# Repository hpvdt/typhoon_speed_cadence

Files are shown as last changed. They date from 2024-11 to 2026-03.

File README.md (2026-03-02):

# Typhoon Speed and Cadence

This is the amazing repository for the amazing Speed and Cadance team.
This embedded system uses an STM32 and a hall effect setup to accurately calculate the speed of the bike in real time, displaying the information to an OLED
HOE: Oliver Cai, Juston Lo
Lead: Daniel Dot
Members: Luca M, Rena, Noah, Iris

MEMBERS ADD YOUR LAST NAMES PLEASE I DONT KNOW THEM :(

## Hardware Setup

We must all operate on the same main version of KiCad, 9.0.
Ensure you are always working on the project file, never open the files standalone.

## Firmware Setup

### THIS PART IS VERY IMPORTANT PLEASE READ

We must all operate on the same versions, if we do not then stuff will break. We are currently using:
- STM32CubeIDE 2.0.0
- STM32CubeMX 6.16.0

You must download both to program as the IDE is used oto program while the CubeMX is for the .ioc file to configure the board pinout.

When writing code in the main.c, main.h, or any program where code is overwritten from the .ioc save, PLEASE ENSURE YOU ARE WRITING IN A USER CODE BLOCK, or else your code will be removed.

The main code is found in main.c in the src folder, and whenever working on the code always work in the project folder, dont open the file standalone. 
The logic for the code is commented in code, and any changes MUST also be commented for others to work simultaneously on it.

If there are any questions about the project, message me on disc dot2944, or email daniel.dot@mail.utoronto.ca

## Organization

Pretty self-explanitory, put hardware related files into the `hardware` folder, firmware in the `firmware` folder. Other folders can be added as needed: for example a `media` folder is handy for storing pictures related to a project which can be used in documentation.

## Conventions

Partly for consistency, partly for functionality; please follow the following conventions:

- Try to keep folder names to single words and all lowercase
- Use underscores to separate words in names (e.g. `board_rev1`). **DO NOT USE SPACES! ESPECIALLY FOR FOLDERS CONTAINING CODE!** Spaces in file paths may cause issues in compilers and such so best to avoid them entirely.

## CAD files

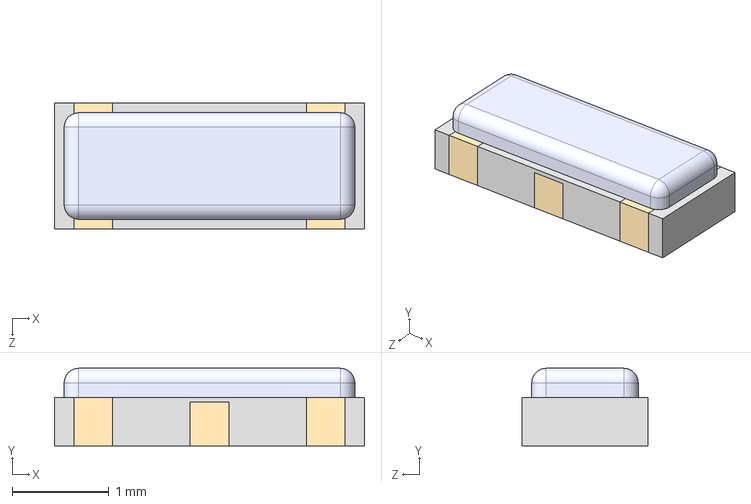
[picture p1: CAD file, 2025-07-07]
hardware/vers_2/CSTNE8M00G52Z000R0/CSTNE8M00G52Z000R0.step
3.20 x 0.8 x 1.30 mm

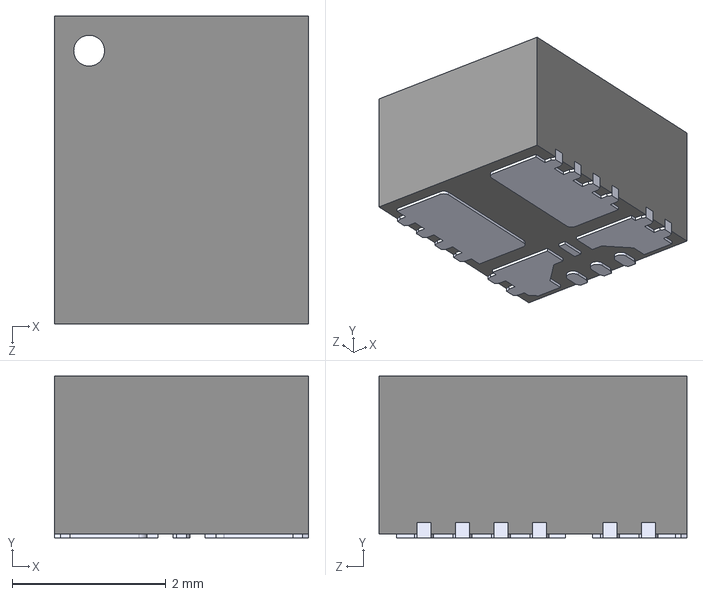
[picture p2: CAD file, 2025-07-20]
hardware/vers_2/TPSM861253RDXR/TPSM861253RDXR.step
3.30 x 2.10 x 4.00 mm

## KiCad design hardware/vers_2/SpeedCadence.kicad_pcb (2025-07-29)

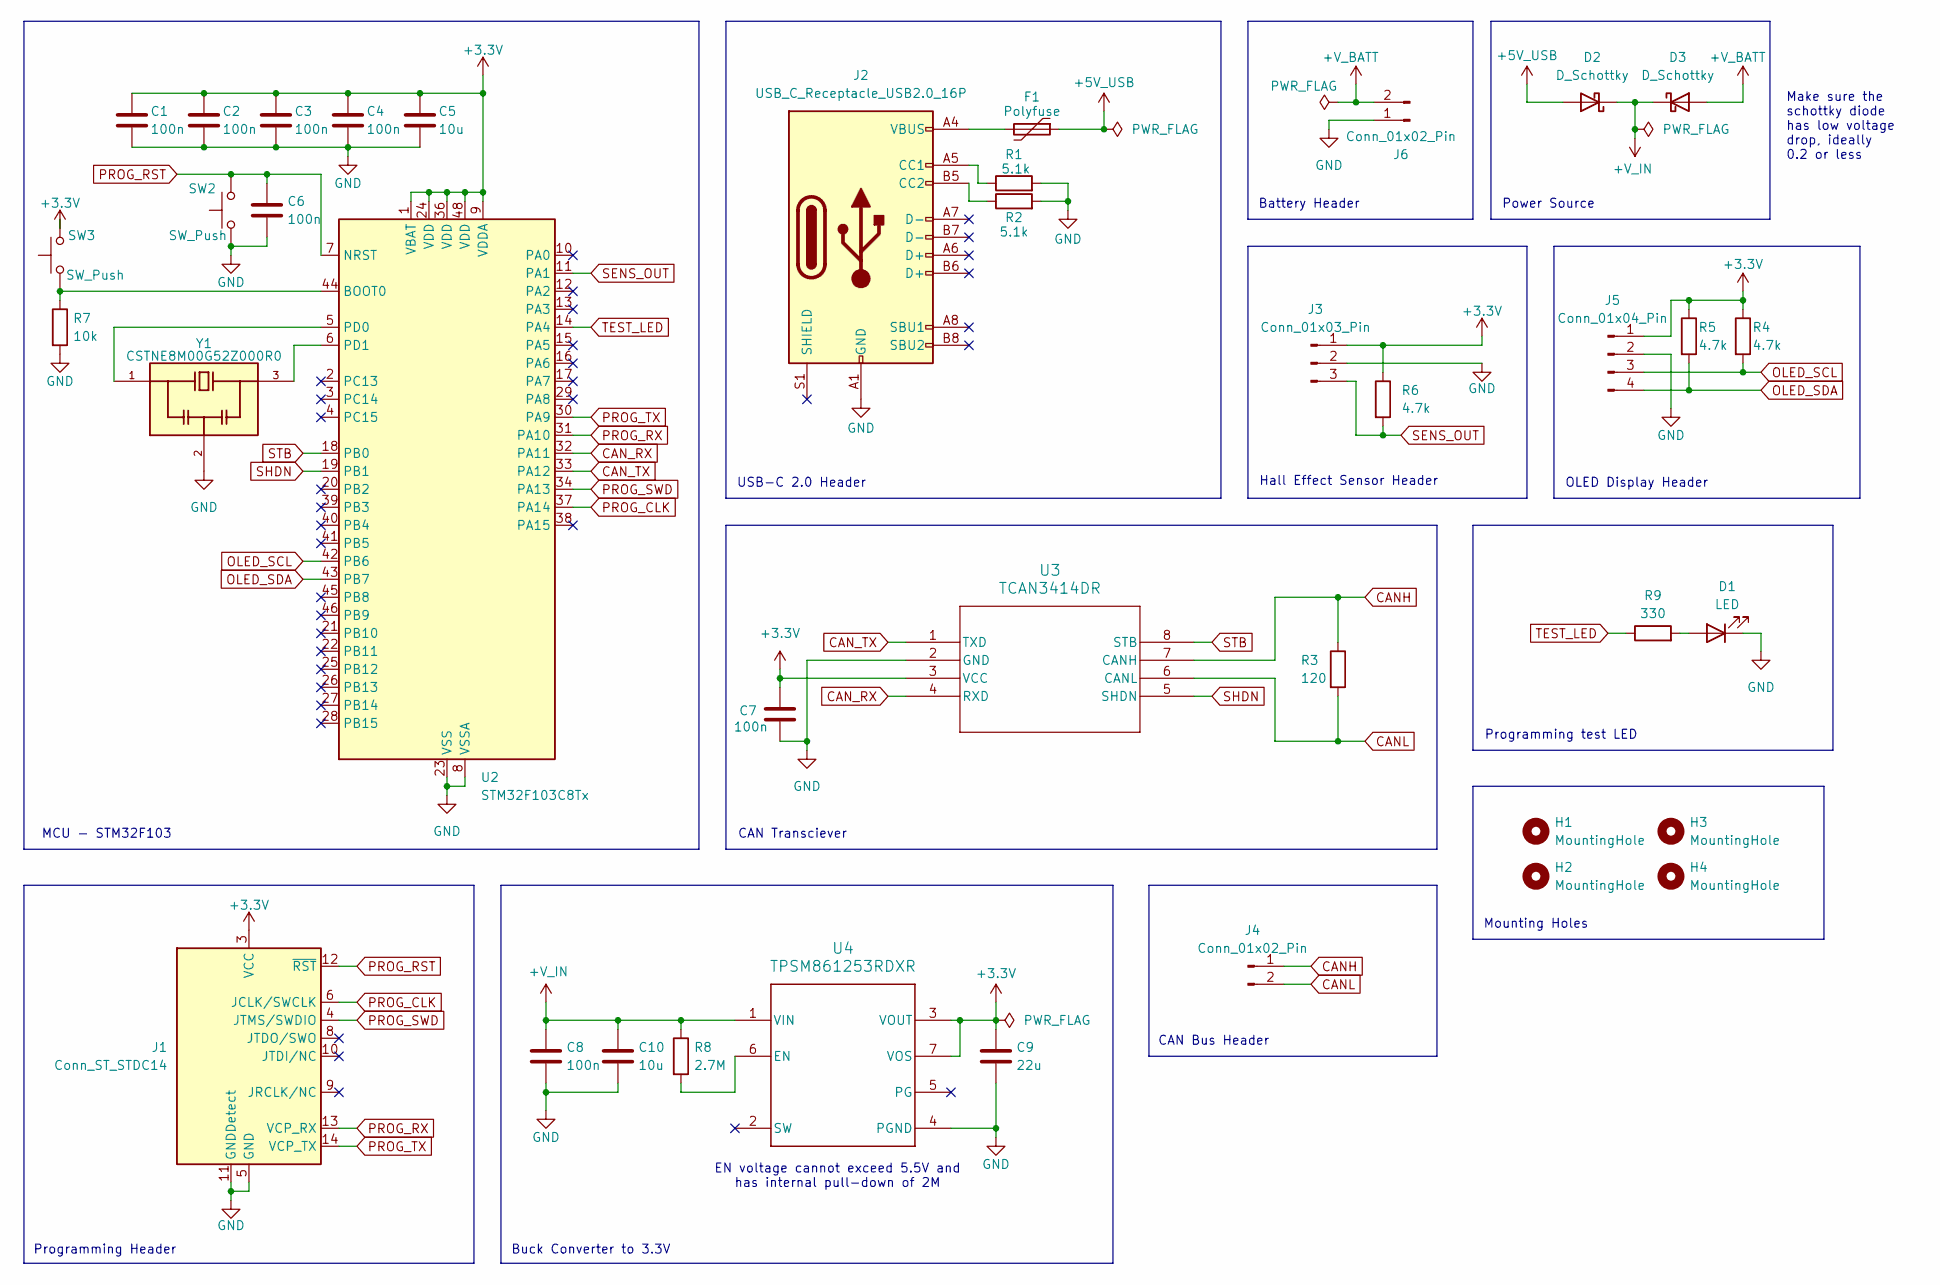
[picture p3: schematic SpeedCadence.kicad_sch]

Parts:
C1, C2, C3, C4, C6, C7, C8: 100n; C_0805_2012Metric; Manufacturer Part Number CC0805KRX7R9BB104
C5, C10: 10u; C_0805_2012Metric; Manufacturer Part Number GRM21BR71A106KA73K
C9: 22u; C_0805_2012Metric; Manufacturer Part Number GRM21BZ71A226ME15L
D1: LED; LED_0805_2012Metric; Manufacturer Part Number 5975906507F
D2, D3: D_Schottky; D_SOD-123; Manufacturer Part Number 1N5819HW-7-F
F1: Polyfuse; Fuse_1206_3216Metric; Manufacturer Part Number 0ZCJ0020FF2E
H1, H2, H3, H4: MountingHole; MountingHole_2.2mm_M2
J1: Conn_ST_STDC14; PinHeader_2x07_P1.27mm_Vertical_SMD; Manufacturer Part Number FTSH-107-01-L-DV-K-A
J2: USB_C_Receptacle_USB2.0_16P; USB_C_Receptacle_JAE_DX07S016JA1R1500; Manufacturer Part Number DX07S016JA3R1500
J3: Conn_01x03_Pin; JST_XH_B3B-XH-A_1x03_P2.50mm_Vertical; Manufacturer Part Number B3B-XH-A(LF)(SN)
J4, J6: Conn_01x02_Pin; JST_XH_B2B-XH-A_1x02_P2.50mm_Vertical; Manufacturer Part Number B2B-XH-A-BK(LF)(SN)
J5: Conn_01x04_Pin; JST_XH_B4B-XH-A_1x04_P2.50mm_Vertical; Manufacturer Part Number B4B-XH-A(LF)(SN)
R1, R2: 5.1k; R_0805_2012Metric; Manufacturer Part Number RC0805JR-075K1L
R3: 120; R_0805_2012Metric; Manufacturer Part Number P0603Y60R0BBT
R4, R5, R6: 4.7k; R_0805_2012Metric
R7: 10k; R_0805_2012Metric
R8: 2.7M; R_0805_2012Metric
R9: 330; R_0805_2012Metric
SW2, SW3: SW_Push; SW_SPST_SKQG_WithStem
U2: STM32F103C8Tx; LQFP-48_7x7mm_P0.5mm
U3: TCAN3414DR; SOIC-8_3.9x4.9mm_P1.27mm
U4: TPSM861253RDXR; VREG_TPSM861253RDXR
Y1: CSTNE8M00G52Z000R0; OSC_CSTNE8M00G52Z000R0; PARTREV JGC42-8858A

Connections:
+3.3V: C1.2, C2.2, C3.2, C4.2, C5.1, C7.1, C9.1, J1.3 (VCC), J3.1, J5.1, R4.1, R5.1, R6.1, SW3.2, U2.1 (VBAT), U2.9 (VDDA), U2.24 (VDD), U2.36 (VDD), U2.48 (VDD), U3.3 (VCC), U4.3 (VOUT), U4.7 (VOS), U4.14, U4.15, U4.16, U4.17, U4.18, U4.19
+5V_USB: D2.2 (A), F1.1
+V_BATT: D3.2 (A), J6.2
+V_IN: C8.1, C10.1, D2.1 (K), D3.1 (K), R8.1, U4.1 (VIN)
CANH: J4.1, R3.1, U3.7 (CANH)
CANL: J4.2, R3.2, U3.6 (CANL)
CAN_RX: U2.32 (PA11), U3.4 (RXD)
CAN_TX: U2.33 (PA12), U3.1 (TXD)
GND: C1.1, C2.1, C3.1, C4.1, C5.2, C6.2, C7.2, C8.2, C9.2, C10.2, D1.1 (K), J1.5 (GND), J1.7 (GND), J1.11 (GNDDetect), J2.A1 (GND), J2.A12 (GND), J2.B1 (GND), J2.B12 (GND), J3.2, J5.2, J6.1, R1.2, R2.2, R7.2, SW2.1, U2.8 (VSSA), U2.23 (VSS), U2.35 (VSS), U2.47 (VSS), U3.2 (GND), U4.4 (PGND), Y1.2
unnamed: D1.2 (A), R9.2
unnamed: F1.2, J2.A4 (VBUS), J2.A9 (VBUS), J2.B4 (VBUS), J2.B9 (VBUS)
unnamed: J2.A5 (CC1), R1.1
unnamed: J2.B5 (CC2), R2.1
unnamed: R7.1, SW3.1, U2.44 (BOOT0)
unnamed: U2.5 (PD0), Y1.1
unnamed: U2.6 (PD1), Y1.3
unnamed: R8.2, U4.6 (EN)
OLED_SCL: J5.3, R4.2, U2.42 (PB6)
OLED_SDA: J5.4, R5.2, U2.43 (PB7)
PROG_CLK: J1.6 (JCLK/SWCLK), U2.37 (PA14)
PROG_RST: C6.1, J1.12 (~RST), SW2.2, U2.7 (NRST)
PROG_RX: J1.13 (VCP_RX), U2.31 (PA10)
PROG_SWD: J1.4 (JTMS/SWDIO), U2.34 (PA13)
PROG_TX: J1.14 (VCP_TX), U2.30 (PA9)
SENS_OUT: J3.3, R6.2, U2.11 (PA1)
SHDN: U2.19 (PB1), U3.5 (SHDN)
STB: U2.18 (PB0), U3.8 (STB)
TEST_LED: R9.1, U2.14 (PA4)

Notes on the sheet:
Mounting Holes
CAN Transciever
MCU - STM32F103
CAN Bus Header
Battery Header
USB-C 2.0 Header
Buck Converter to 3.3V
Power Source
Hall Effect Sensor Header
EN voltage cannot exceed 5.5V and has internal pull-down of 2M
OLED Display Header
Programming Header
Programming test LED
Make sure the schottky diode has low voltage drop, ideally 0.2 or less

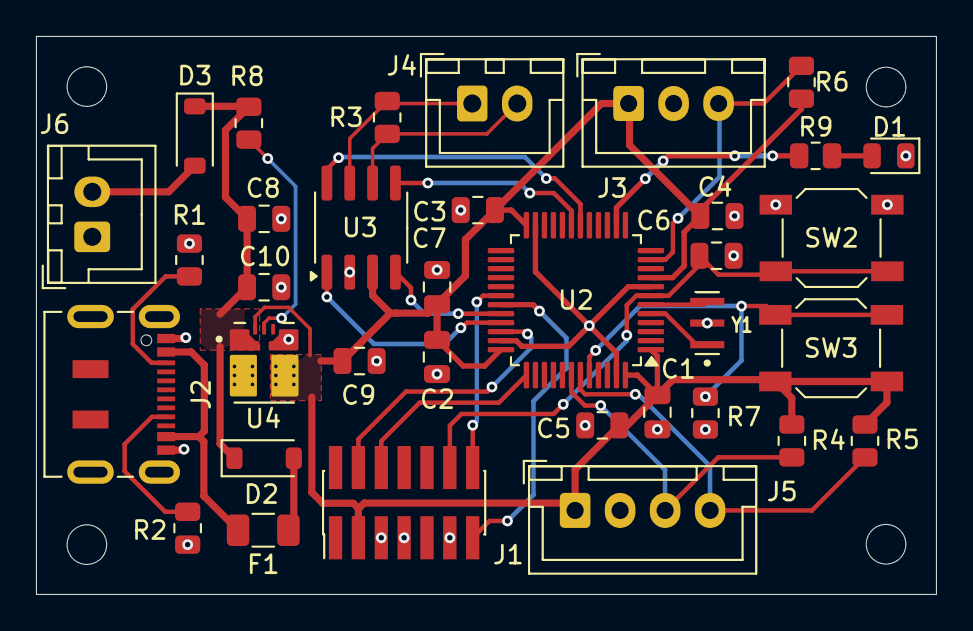
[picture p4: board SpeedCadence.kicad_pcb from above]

Board: 2 copper layers, 50.0 x 31.0 mm, 39 parts (0 on the bottom side), 28 nets.

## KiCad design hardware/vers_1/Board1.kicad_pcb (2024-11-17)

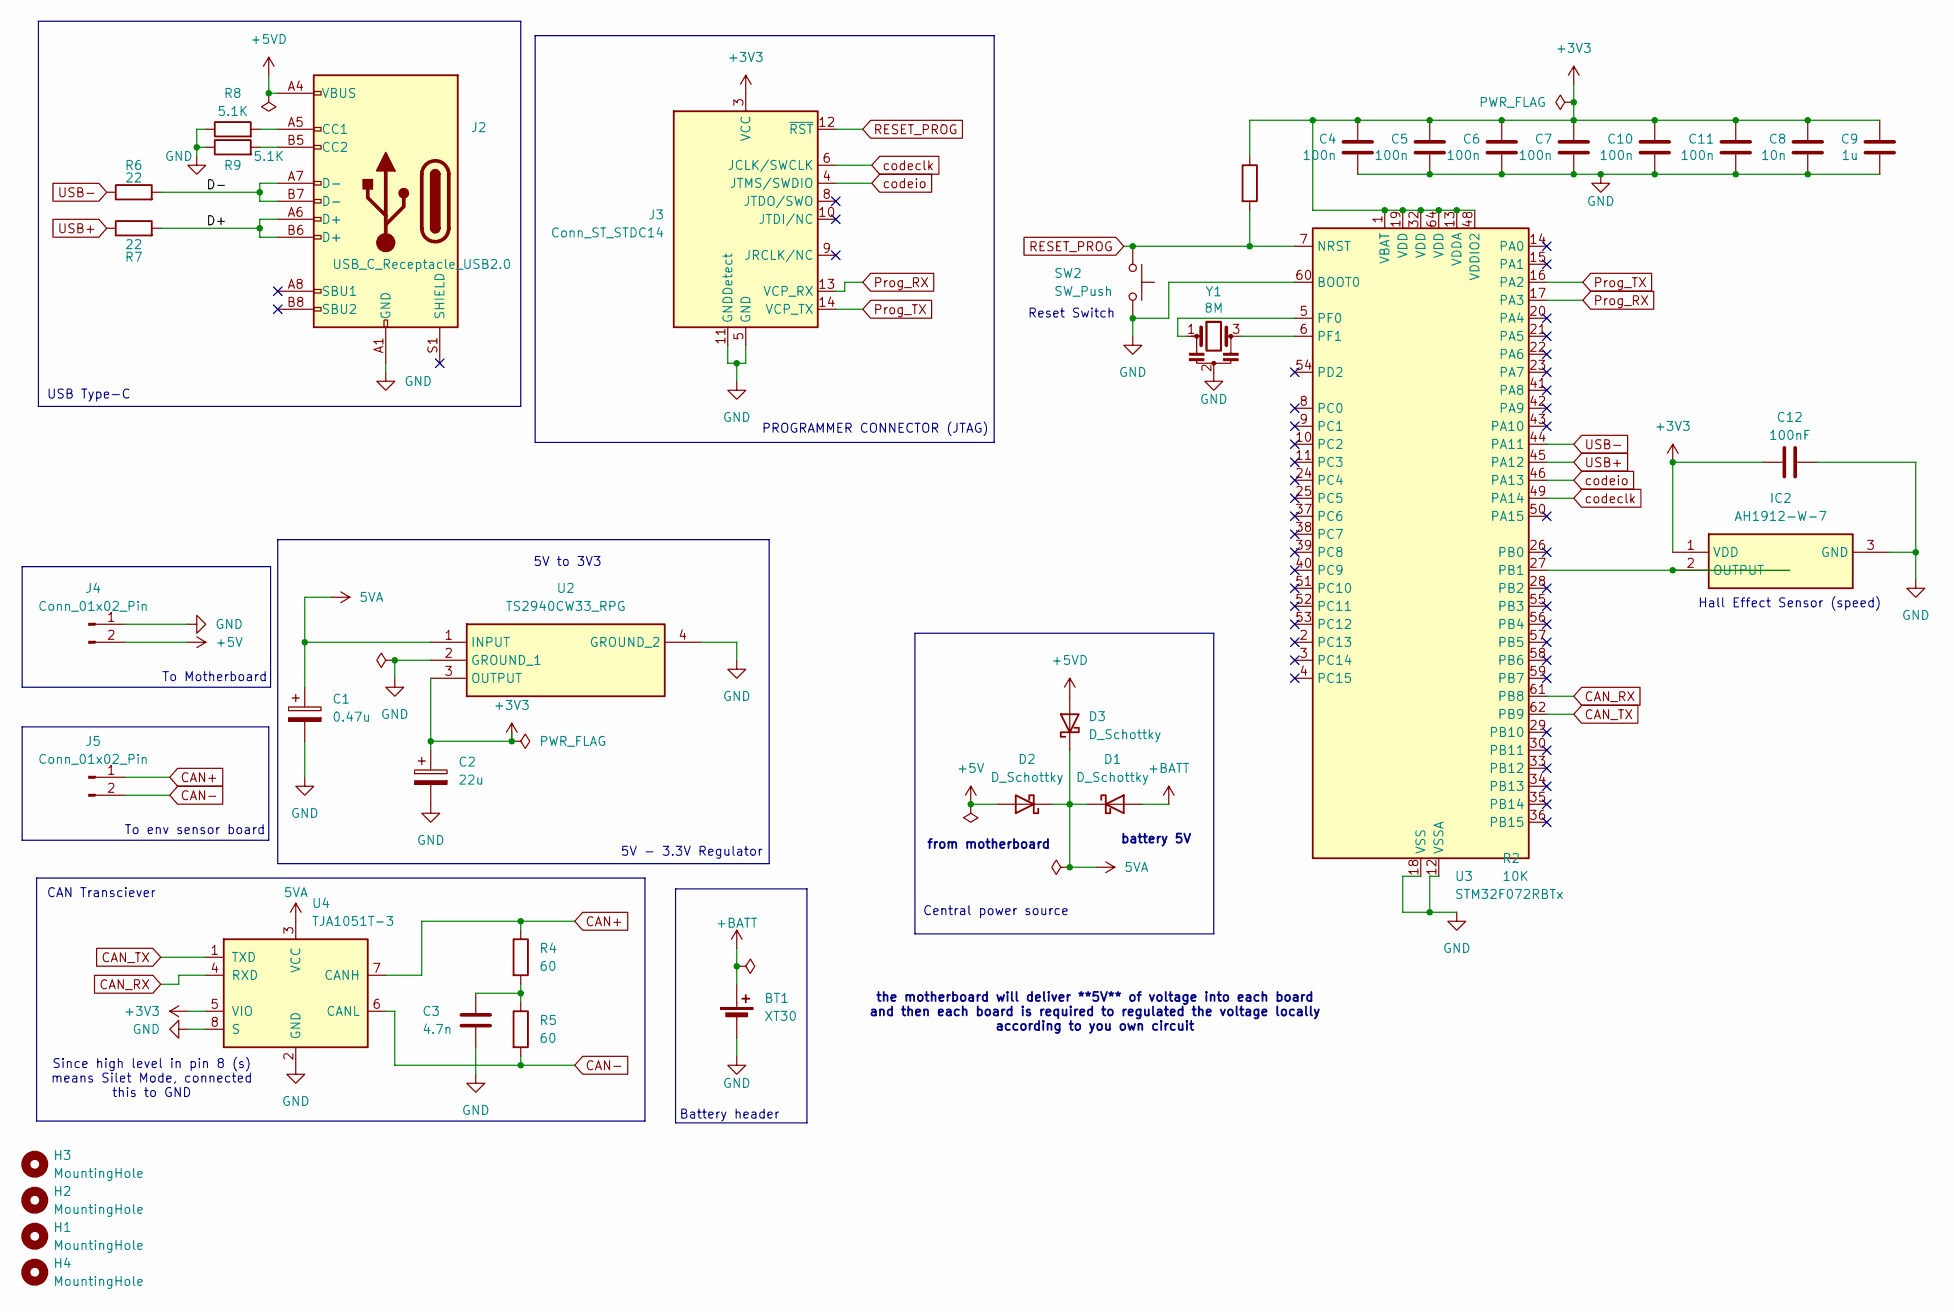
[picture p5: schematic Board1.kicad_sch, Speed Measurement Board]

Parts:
BT1: XT30; AMASS_XT30PW-M_1x02_P2.50mm_Horizontal
C1: 0.47u; C_1206_3216Metric
C2: 22u; C_1206_3216Metric
C3: 4.7n; C_0603_1608Metric
C4, C5, C6, C7, C10, C11: 100n; C_0603_1608Metric
C8: 10n; C_0603_1608Metric
C9: 1u; C_0603_1608Metric
C12: 100nF; C_0603_1608Metric
D1, D2, D3: D_Schottky; D_SOD-123
H1, H2, H3, H4: MountingHole; MountingHole_3.2mm_M3_ISO14580
IC2: AH1912-W-7; SC-59; Mouser Part Number 621-AH1912-W-7
J2: USB_C_Receptacle_USB2.0; USB_C_Receptacle_HRO_TYPE-C-31-M-12
J3: Conn_ST_STDC14; PinHeader_2x07_P1.27mm_Vertical_SMD
J4, J5: Conn_01x02_Pin; JST_EH_S2B-EH_1x02_P2.50mm_Horizontal
R2: 10K; R_0603_1608Metric
R4, R5: 60; R_0603_1608Metric
R6, R7: 22; R_0603_1608Metric
R8, R9: 5.1K; R_0603_1608Metric
SW2: SW_Push; SW_SPST_SKQG_WithStem
U2: TS2940CW33_RPG; SOT-223-3_TabPin2; Mouser Part Number 821-TS2940CW33RPG
U3: STM32F072RBTx; LQFP-64_10x10mm_P0.5mm
U4: TJA1051T-3; SOIC-8_3.9x4.9mm_P1.27mm
Y1: 8M; Resonator_SMD_Murata_CSTxExxV-3Pin_3.0x1.1mm

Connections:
5VA: C1.1, D1.1 (K), D2.1 (K), D3.1 (K), U2.1 (INPUT), U4.3 (VCC)
+3V3: C2.1, C4.2, C5.2, C6.2, C7.2, C8.2, C9.2, C10.2, C11.2, C12.1, IC2.1 (VDD), J3.3 (VCC), R2.1, U2.3 (OUTPUT), U3.1 (VBAT), U3.13 (VDDA), U3.19 (VDD), U3.32 (VDD), U3.48 (VDDIO2), U3.64 (VDD), U4.5 (VIO)
+5V: D2.2 (A), J4.2
+5VD: D3.2 (A), J2.A4 (VBUS), J2.A9 (VBUS), J2.B4 (VBUS), J2.B9 (VBUS)
+BATT: BT1.1 (+), D1.2 (A)
/D+: J2.A6 (D+), J2.B6 (D+), R7.2
/D-: J2.A7 (D-), J2.B7 (D-), R6.2
CAN+: J5.1, R4.1, U4.7 (CANH)
CAN-: J5.2, R5.2, U4.6 (CANL)
CAN_RX: U3.61 (PB8), U4.4 (RXD)
CAN_TX: U3.62 (PB9), U4.1 (TXD)
GND: BT1.2 (-), C1.2, C2.2, C3.2, C4.1, C5.1, C6.1, C7.1, C8.1, C9.1, C10.1, C11.1, C12.2, IC2.3 (GND), J2.A1 (GND), J2.A12 (GND), J2.B1 (GND), J2.B12 (GND), J3.5 (GND), J3.7 (GND), J3.11 (GNDDetect), J4.1, R8.1, R9.1, SW2.2, U2.2 (GROUND_1), U2.4 (GROUND_2), U3.12 (VSSA), U3.18 (VSS), U3.31 (VSS), U3.47 (VSS), U3.60 (BOOT0), U3.63 (VSS), U4.2 (GND), U4.8 (S), Y1.2; also elsewhere on the board
unnamed: C3.1, R4.2, R5.1
unnamed: IC2.2 (OUTPUT), U3.27 (PB1)
unnamed: J2.A5 (CC1), R8.2
unnamed: J2.B5 (CC2), R9.2
unnamed: U3.5 (PF0), Y1.1
unnamed: U3.6 (PF1), Y1.3
Prog_RX: J3.13 (VCP_RX), U3.17 (PA3)
Prog_TX: J3.14 (VCP_TX), U3.16 (PA2)
RESET_PROG: J3.12 (~RST), R2.2, SW2.1, U3.7 (NRST)
USB+: R7.1, U3.45 (PA12)
USB-: R6.1, U3.44 (PA11)
codeclk: J3.6 (JCLK/SWCLK), U3.49 (PA14)
codeio: J3.4 (JTMS/SWDIO), U3.46 (PA13)

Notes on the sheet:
To Motherboard
Reset Switch
PROGRAMMER CONNECTOR (JTAG)
Battery header
USB Type-C
5V to 3V3
Central power source
battery 5V
CAN Transciever
the motherboard will deliver **5V** of voltage into each board and then each board is required to regulated the voltage locally according to you own circuit
from motherboard
Hall Effect Sensor (speed)
Since high level in pin 8 (s) means Silet Mode, connected this to GND
To env sensor board
5V - 3.3V Regulator

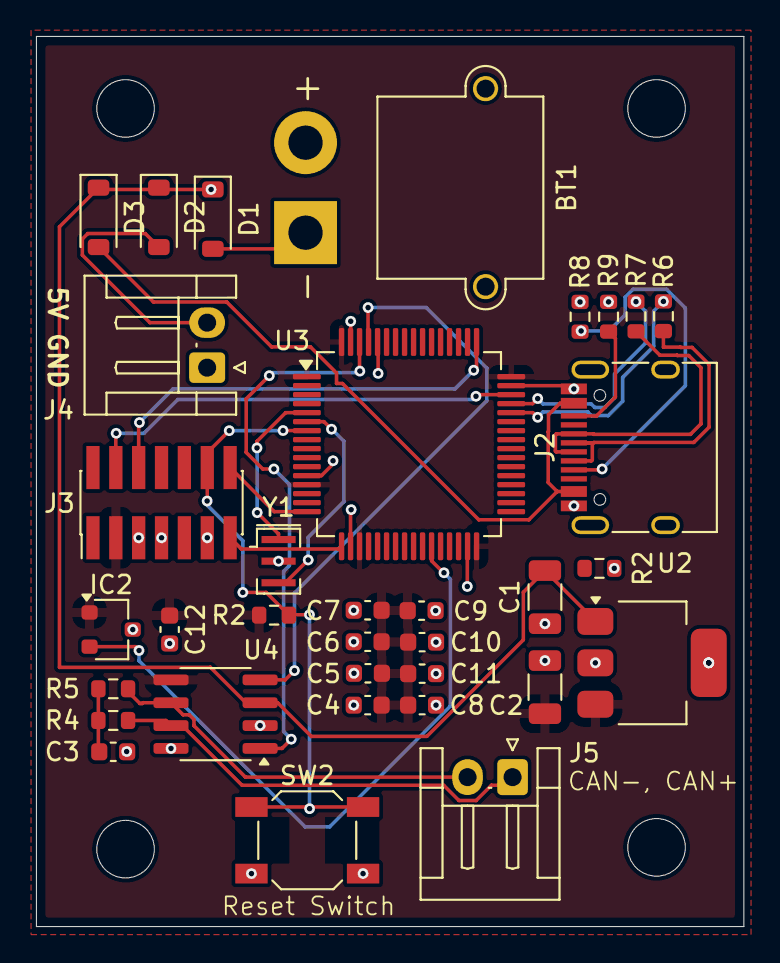
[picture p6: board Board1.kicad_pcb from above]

Board: 2 copper layers, 39.3 x 49.4 mm, 38 parts (0 on the bottom side), 25 nets.

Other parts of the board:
R2#2: 5.1k; R_0603_1608Metric

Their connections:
GND: R2#2.2; also elsewhere on the board

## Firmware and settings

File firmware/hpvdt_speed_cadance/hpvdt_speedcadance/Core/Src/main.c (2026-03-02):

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
/* Includes ------------------------------------------------------------------*/
#include "main.h"

/* USER CODE BEGIN Includes */
#include "ssd1306.h"
#include "ssd1306_fonts.h"
#include <stdio.h>
/* USER CODE END Includes */

/* USER CODE BEGIN PD */
//Average size of the rolling average
#define AVG_SIZE 8
#define WHEEL_RADIUS_MM 325.5f //(DIMENSIONS IN MM)
#define PI 3.14159265f
#define magnet_count 1 //Accounts for the amount of magnets placed on the wheel
#define RPM_TO_KMH_FACTOR ((2.0f * PI * WHEEL_RADIUS_MM * 60.0f) / 1000000.0f)
/* USER CODE END PD */

I2C_HandleTypeDef hi2c1;

/* USER CODE BEGIN PV */
// Use volatile so the compiler knows it changes in an ISR, Flag Variables
volatile uint8_t magnet_flag = 0;
volatile uint32_t pulse_time = 0;

//Calculation variables
uint32_t time_diffs[AVG_SIZE] = {0};
float speed_kmh = 0.0f;
uint8_t avg_index = 0;
uint32_t last_time = 0;
uint32_t last_display_time = 0;
float filtered_rpm = 0.0f;
uint8_t samples_collected = 0;
uint32_t running_sum = 0;
/* USER CODE END PV */

void SystemClock_Config(void);
static void MX_GPIO_Init(void);
static void MX_I2C1_Init(void);
/**
  * @brief  The application entry point.
  * @retval int
  */
int main(void)
{

  /* MCU Configuration--------------------------------------------------------*/

  /* Reset of all peripherals, Initializes the Flash interface and the Systick. */
  HAL_Init();

  /* Configure the system clock */
  SystemClock_Config();

  /* Initialize all configured peripherals */
  MX_GPIO_Init();
  MX_I2C1_Init();
  /* USER CODE BEGIN 2 */
  //Initializes the first text to the I2C display
  ssd1306_Init();
  ssd1306_SetCursor(5,5);
  ssd1306_WriteString("SPEED: ", Font_11x18, White);
  ssd1306_SetCursor(5,24);
  ssd1306_WriteString("RPM: ", Font_11x18, White);
  ssd1306_UpdateScreen();
  /* USER CODE END 2 */

  /* Infinite loop */
  /* USER CODE BEGIN WHILE */
  while (1)
  {
	  //----------------------------------------------------------
	  // 1. MAGNET FLAG PROCESSING
	  //----------------------------------------------------------

	  //Get the current time as a reference
	  uint32_t now = HAL_GetTick();

	  //If the flag for the magnet was triggered
	  if (magnet_flag)
	  {
		  // Snapshot the time safely and reset the flag ensuring no other magnet pulse affects it
		  __disable_irq();
		  uint32_t current_pulse = pulse_time;
		  magnet_flag = 0;
		  __enable_irq();

		  if (last_time != 0)
		  {
			  uint32_t diff = current_pulse - last_time;

			  // Debounce: Ignore pulses faster than 3000 RPM (20ms)
			  if (diff > 20)
			  {
				  // 1. Subtract the OLD value from the running sum
				  running_sum -= time_diffs[avg_index];

				  // 2. Store the NEW value in the circular buffer
				  time_diffs[avg_index] = diff;

	  			  // 3. Add the NEW value to the running sum
	  			  running_sum += time_diffs[avg_index];

	  			  avg_index = (avg_index + 1) % AVG_SIZE;

	  			  if (samples_collected < AVG_SIZE)
	  				  samples_collected++;
			  }
	  		}

	  		// ALWAYS update last_time so the next pulse has a reference
	  		last_time = current_pulse;
	  	  }

	  	//----------------------------------------------------------
	  	// 2. TIMED DISPLAY & CALCULATIONS (Every 300ms)
	  	//----------------------------------------------------------

	  	if (now - last_display_time >= 300)
	  	{
	  		last_display_time = now;

	  	     // Timeout: If no magnet seen for 2.5 seconds, we are stopped
	  	     if (last_time != 0 && (now - last_time > 2500))
	  	     {
	  	    	 filtered_rpm = 0.0f;
	  	    	 speed_kmh = 0.0f;
	  	         samples_collected = 0;
	  	         running_sum = 0;
	  	         last_time = 0; // Require a fresh first pulse to start again

	  	         for(int i = 0; i < AVG_SIZE; i++)
	  	        	 time_diffs[i] = 0;
	  	     }

	  	     else if (samples_collected > 0)
	  	     {
	  	         // Formula: (RPM * 2 * PI * R * 60) / 1,000,000
	  	    	 filtered_rpm = (60000.0f * (float)samples_collected) / (float)running_sum;
	  	         speed_kmh = filtered_rpm * RPM_TO_KMH_FACTOR;
	  	     }

	  	     // Update the OLED screen
	  	     char buffer[25];
	  	     sprintf(buffer, "%.2f km/h  ", speed_kmh);

	  	     ssd1306_SetCursor(68, 5);
	  	     ssd1306_WriteString(buffer, Font_11x18, White);

	  	     sprintf(buffer, "%.2f RPM  ", filtered_rpm);
	  	     ssd1306_SetCursor(45, 24);
	  	     ssd1306_WriteString(buffer, Font_11x18, White);
	  	     ssd1306_UpdateScreen();
	  	}

    /* USER CODE END WHILE */

    /* USER CODE BEGIN 3 */

  }
  /* USER CODE END 3 */
}

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
/* USER CODE BEGIN 4 */

//---------------------------------------------------------
//CALLBACK LOGIC FOR THE MAGNET FLAG
//--------------------------------------------------------

void HAL_GPIO_EXTI_Callback(uint16_t GPIO_Pin)
{
    if (GPIO_Pin == HALLEFFECT_PIN_Pin)
    {
        pulse_time = HAL_GetTick(); // Get the time the microsecond it happened
        magnet_flag = 1;            // Set the flag for the main loop

        // Quick visual feedback (Keep this very fast)
        HAL_GPIO_TogglePin(LED_GPIO_Port, LED_Pin);
    }
}
/* USER CODE END 4 */
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


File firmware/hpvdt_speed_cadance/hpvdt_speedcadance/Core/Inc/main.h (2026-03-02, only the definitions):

#define RESONATOR_IN_Pin GPIO_PIN_0
#define RESONATOR_IN_GPIO_Port GPIOD
#define RESONATOR_OUT_Pin GPIO_PIN_1
#define RESONATOR_OUT_GPIO_Port GPIOD
#define HALLEFFECT_PIN_Pin GPIO_PIN_1
#define HALLEFFECT_PIN_GPIO_Port GPIOA
#define HALLEFFECT_PIN_EXTI_IRQn EXTI1_IRQn
#define LED_Pin GPIO_PIN_4
#define LED_GPIO_Port GPIOA
#define OLED_SCL_Pin GPIO_PIN_6
#define OLED_SCL_GPIO_Port GPIOB
#define OLED_SDA_Pin GPIO_PIN_7
#define OLED_SDA_GPIO_Port GPIOB

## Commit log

2024-10-14 Updated with comments
    [Board1.kicad_pcb, Board1.kicad_sch]
2024-10-18 Updated differential pair fill zone
    [Board1.kicad_pcb]
2024-10-18 Comments Added
    [Board1.kicad_sch]
2024-10-31 Modified Schematic according to comments/meeting
    [Board1.kicad_sch]
2024-10-31 Updated board schematic with comments
    [Board1.kicad_sch]
2024-11-15 Made a few changes regarding STM32
    [Board1.kicad_pcb, Board1.kicad_sch]
2024-11-16 added order details (not finalised)
    [Board1.kicad_pcb]
2024-11-17 final revision of the speed and cadence board
    Finished re routing the PCB and also did BOM and production needed for JLC PCB
    [Board1.kicad_pcb, Board1.kicad_sch]
2024-11-17 Final small changes, only silkscreen stuff
    [Board1.kicad_pcb, Board1.kicad_sch]
2025-07-07 Added version 2
    [Board1.kicad_pcb, Board1.kicad_sch, CSTNE8M00G52Z000R0.step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]
2025-07-07 Revision 2
    [Board1.kicad_pcb, Board1.kicad_sch, CSTNE8M00G52Z000R0.step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]
2025-07-08 Updated LDO
    [SpeedCadence.kicad_sch]
2025-07-08 PCB design complete
    [SpeedCadence.kicad_pcb, SpeedCadence.kicad_sch]
2025-07-08 Small adjustment
    [SpeedCadence.kicad_pcb]
2025-07-10 Comments for vers2
    [SpeedCadence.kicad_sch]
2025-07-10 Fixed minor changes
    [SpeedCadence.kicad_pcb, SpeedCadence.kicad_sch]
2025-07-11 removed tvs diode
    [SpeedCadence.kicad_pcb, SpeedCadence.kicad_sch]
2025-07-11 R3, R4 changed to 0603 footprint
    [SpeedCadence.kicad_pcb, SpeedCadence.kicad_sch]
2025-07-20 Changed to 6.4V with buck converter
    [SpeedCadence.kicad_pcb, SpeedCadence.kicad_sch, TPSM861253RDXR.step]
2025-07-21 minor changes
    [SpeedCadence.kicad_pcb, SpeedCadence.kicad_sch]
2025-07-25 test LED and USB footprint change
    [SpeedCadence.kicad_pcb, SpeedCadence.kicad_sch]
2025-07-29 Changed termination on CAN lines from 60 ohm to 120 ohm
    [SpeedCadence.kicad_pcb, SpeedCadence.kicad_sch]
2025-07-29 Added manufacturers and manufacturer part numbers
    [SpeedCadence.kicad_sch]
2025-07-29 Small change to labels
    [SpeedCadence.kicad_sch]
2026-02-04 Added Blinky Code
    Found out there was a bug regarding programming the project. Just started a new one isntead
    [main.c, main.h]
2026-02-10 Added CAN prototype code (did not work)
    [main.c, main.h, typhoon_speed_cadence_can_prot.ioc]
2026-03-02 Changed Clock Config and Switched to Interrupt Driven Logic
    Justin Lo (STD) I changed your clock config as well to work with the external 32MHz so for your CAN and UART consider this

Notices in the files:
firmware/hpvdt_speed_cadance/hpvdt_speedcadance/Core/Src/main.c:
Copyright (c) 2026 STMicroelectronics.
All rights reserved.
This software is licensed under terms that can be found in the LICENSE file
